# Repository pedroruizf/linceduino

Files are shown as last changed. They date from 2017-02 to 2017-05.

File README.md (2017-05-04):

# LINCEDUINO
Desarrollo de linceduino, ayuda electrónica del lince.
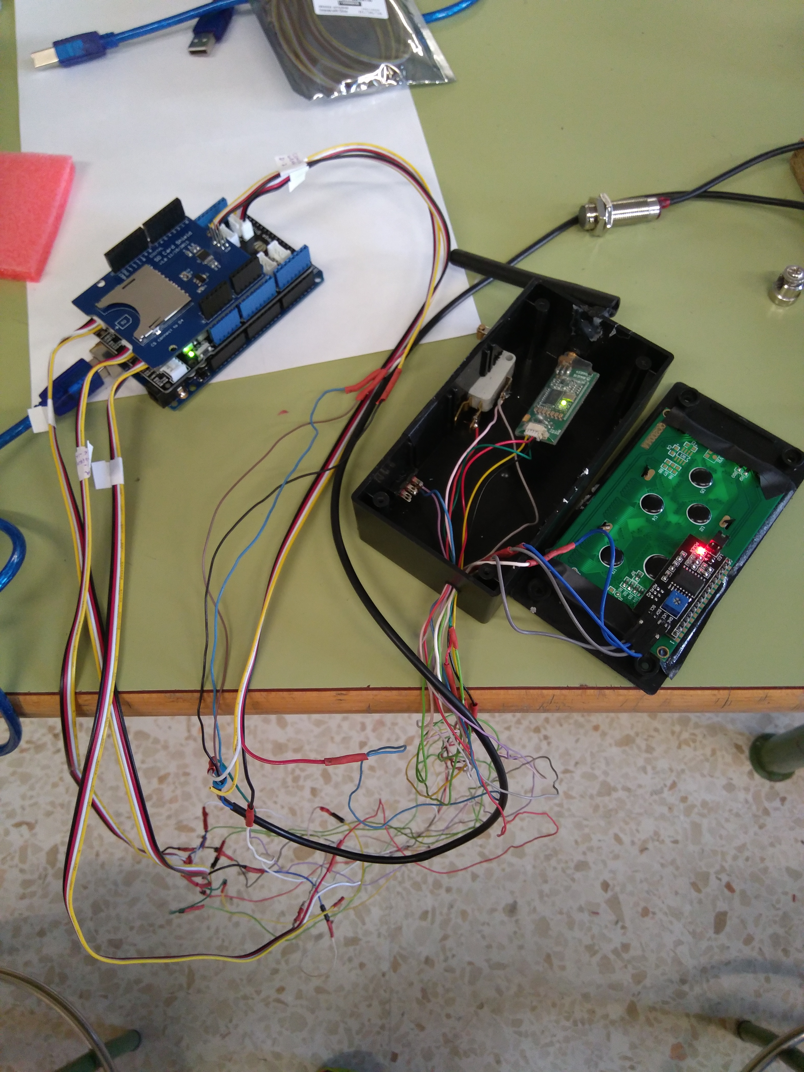
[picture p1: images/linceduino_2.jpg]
linceduino 2 linceduino2


## Objetivo

El objetivo de linceduino es proporcionar una herramienta que ayude al piloto y al equipo del LINCE a tener información en tiempo real y guardada en fichero de parámetros del vehículo como: tiempo transcurrido, velocidad instantánea, velocidad media, distancia, nº de vuelta y pulsación del botón de encendido de motor. Los datos se muestran en pantalla del piloto (lcd 20x4) se guardan en tarjeta SD y se transmiten mediante radiofrecuencia a PC.

## Hardware
Elementos físicos y conexionado:
- Arduino Mega.
- SD Shield.
- [Emisor de radiofrecuencia tipo 3DR Robotics](https://www.amazon.es/SODIAL-Telemetria-Quadcopter-Multirotor-robotica/dp/B0171NHADI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)   (con receptor a PC): rojo (5v), negro (gnd), amarillo (pin 17 RX2), verde (pin 16 TX2).
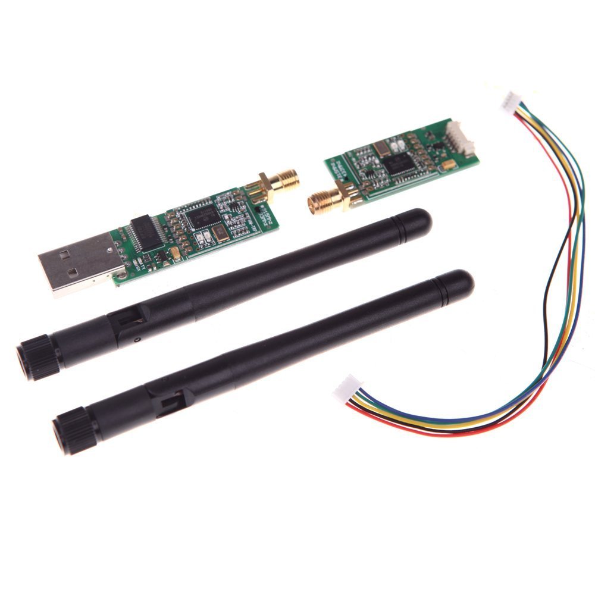
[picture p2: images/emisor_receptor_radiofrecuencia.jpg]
Emisor receptor radiofrecuencia

- LCD I2C 20x4: GND (gnd), VCC (5v), SDA (pin 20), SCL (pin 21).
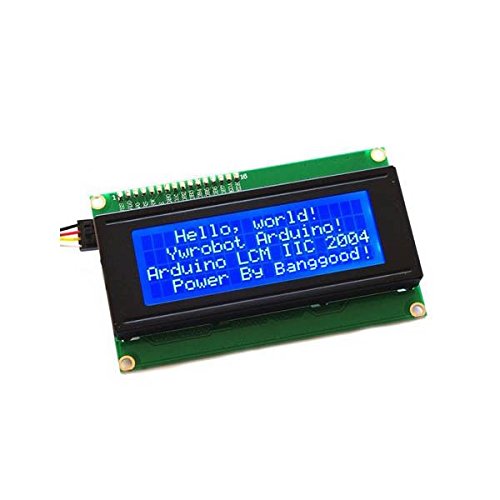
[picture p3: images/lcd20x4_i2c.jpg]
lcd 20x4 i2c lc2 20x4 i2c

- Pulsador de marcha con resistencia de 10 K en serie: pata de pulsador a 5V, la otra a pin 19, resistencia una pata a pin 19 y la otra a GND.
- Conmutador de grabación y resistencia de 10K: Conmutador común a pin 7, otra pata del conmutador a 5v, resistencia de 10 K a pin y la otra pata de la resistencia a GND.
- Sensor magnético Hall: Negro a pin 2, marrón a 5V y azul a GND.
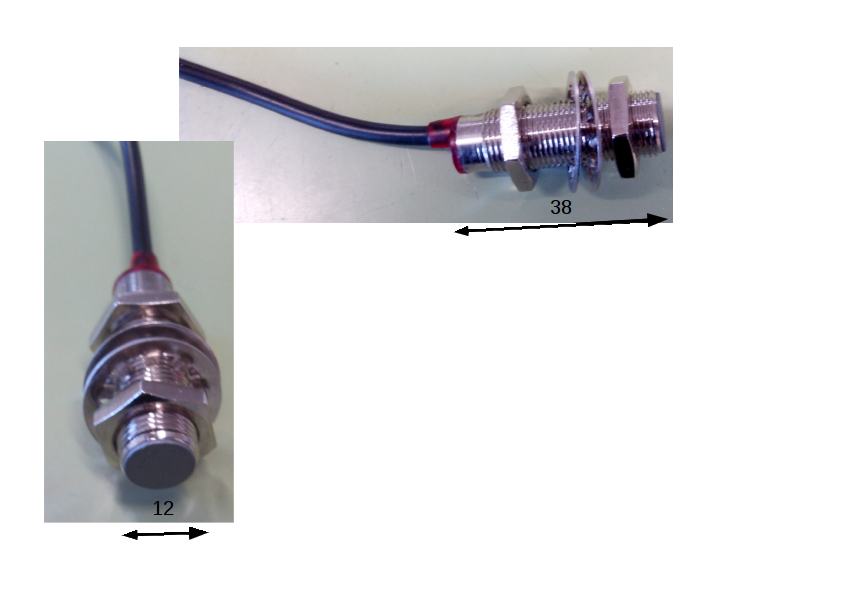
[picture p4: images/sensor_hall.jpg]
sensor hall

Además hemos comprado para realizar un conexionado más seguro un shield conectar y listo (tienda electan) con cables para que el conexionado de todos los elementos sea mucho más seguro.
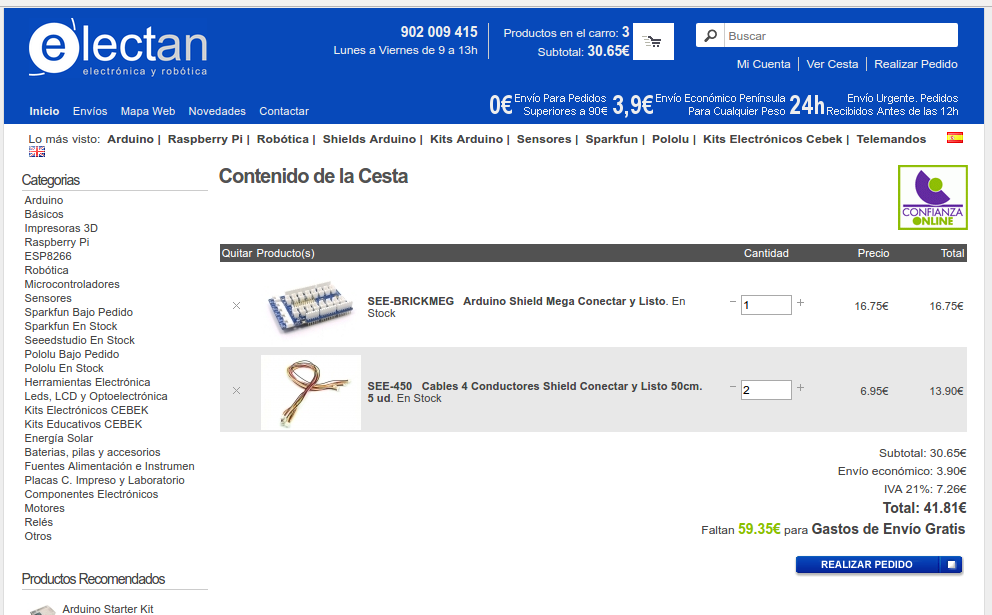
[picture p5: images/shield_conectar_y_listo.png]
Shield conectar y listo Shield Conectar y listo


### Montaje de Linceduino
<iframe width="854" height="480" src="https://www.youtube.com/embed/O8orDAbzBl0" frameborder="0" allowfullscreen></iframe>

## Software
Antes de nada tener un ordenador con ubuntu instalado.
Instalar en el las aplicaciones arduino, kst y Gtkterm, estas aplicaciones están en el centro de software.
Descripción de aplicaciones:
- Arduino: software para programar nuestro arduino Mega.
- Gtkterm: grabador y visualizador de comunicaciones por puerto serie, puerto por el que manda y recibe datos nuestro emisor y receptor de radiofrecuencia.
- KST: representador de datos en tiempo real a través de los datos recogidos en un fichero por Gtkterm.
En nuestro arduino además debemos de agregar una librería para poder operar con nuestro lcd 20x4 (20 columnas 2 filas) de tipo I2C (sólo necesita 4 cables, 2 de alimentación y 2 de datos).

### Programa de Arduino. Linceduino 2.2
~~~
#include <SPI.h>
#include <math.h>
#include <SD.h>
#include <Wire.h>  // Comes with Arduino IDE
#include <LiquidCrystal_I2C.h>
LiquidCrystal_I2C lcd(0x3F, 2, 1, 0, 4, 5, 6, 7, 3, POSITIVE);  // Set the LCD I2C address de 20x4

#define REFRESCO_SD 4 //Frecuencia de guardado
#define pinsd 4 // pin que marca el fabricante de SD Shield
Sd2Card card;// defino una variable card com Sd2CArd
float desarrollo=1492.6; // desarrollo de una vuelta del lince en mm
volatile float tiempopaso, tiempovuelta;//tiempo (hasta la activación del sensor y de una vuelta)
volatile float velocidad, velocidadm; //velocidades (instantánea y media)
volatile float distancia; //distancia recorrida desde que empieza a circular
volatile int lineasBuffer = 0; // lineas de buffer guardadas
volatile int nvueltas = 0; //vuelta de rueda
volatile bool marcha=false;// estado de pulsador de impulso
volatile long ultimamarcha=0;//tiempo que se pulso por ultima vez marcha
String minutos, segundos; //minutos y segundos desde el inicio
char s_string [10];
char m_string [10];
unsigned long tiempo1=0; //tiempo inicial
int vueltas; //vuelta del circuito
String buffer=""; // Almacenamiento temporal de datos recogidos de ISR, para la tarjeta SD
volatile int botonpulsado;// Botón para guardado
File dataFile; //Fichero para guardar datos
bool c = true; //Booleano para la representación

void setup() {

attachInterrupt(0, calculos, RISING);//pin de interrupción 2 arduino mega para sensor hall
attachInterrupt(4, calculosmarcha, CHANGE);//pin de interrupción 19 arduino mega: marcha
lcd.begin(20, 4); //iniciamos la pantalla lcd
lcd.setBacklight(1);
//lcd.backlight ();//da luz al fondo de pantalla de lcd
lcd.clear();
pinMode(pinsd, OUTPUT);
SD.begin(pinsd);//inicializa la SD (tiene que estar insertada) sólo lo hace una vez
lcd.setCursor(0,1);// pone el lcd en la posicion 0,1
if (card.init(SPI_HALF_SPEED, pinsd)) {    
  lcd.print("Tarjeta SD preparada");}
    // don't do anything more:
  //return;
 else {lcd.print("SD error o no inser.");}
lcd.setCursor (1,2); lcd.print ("(: VAMOS LINCE ;)");
delay (4000);
lcd.clear();
Serial2.begin (57600);//comunicacion por puerto serie2 de radiofrecuencia
//Serial.begin (9600);

}

void calculos() {
//Calcula los datos a representar
if (nvueltas==1) {tiempo1=millis();}
nvueltas++;
tiempovuelta=millis()-tiempopaso;//tiempo por vuelta
tiempopaso=millis();//tiempo desde que se produjo la interrupcion
velocidad=(desarrollo*3.6)/tiempovuelta; // (km/h), [mm/ms*3,6 para pasar a km/h]
velocidadm=(desarrollo*3.6*nvueltas)/(millis() - tiempo1);
distancia=(nvueltas*desarrollo)/1000000; //distancia total (km)
vueltas= int((distancia)/1.659)+1; // el circuito tiene 1659 m= 1.659 Km
//solo guarda en buffer y por tanto guarda en fichero cuando si se ha pulsado el boton select
if(botonpulsado==1 && nvueltas>2) {
guardabuffer();
}
}

void calculosmarcha() {
//Interrupción para pulsador 'marcha'
if ((millis()-ultimamarcha)>100 ) {
marcha=!marcha;
ultimamarcha=millis();
if(botonpulsado==1) {
guardabuffer();}
}
}

void guardabuffer(){
//Guarda los datos temporalmente en un buffer
   buffer += String(int((millis()-tiempo1)/1000));buffer += ";";
   buffer += nf(velocidad,2,2);buffer += ";";
   buffer += nf(velocidadm,2,2);buffer += ";";
   buffer += nf(distancia,2,2);buffer += ";";
   buffer += vueltas;buffer += ";";
   buffer += marcha;buffer += "\n";
   lineasBuffer++;
}

void guardasd(){
//Guarda el buffer en un archivo
//SD.begin(pinsd);//inicializa la sd debe estar insertada
dataFile = SD.open("log0.txt", FILE_WRITE);

if (dataFile) {
dataFile.print(buffer);
//lineasBuffer = 0;
//buffer = "";
dataFile.close();
lcd.setCursor(16,0);
c = !c;
if(c) {lcd.print("|");}

else {lcd.print("-");}
}
else {}
}

String nf(float n, int cifras, int decimales) {// la funcion nf tiene como entrada una variable float, el numero de cifras enteras, y el numero de cifras decimales
char numero [10];//creamos la variable tipo char numero de longitud 10
return dtostrf(n,(cifras+decimales+1),decimales,numero);//dtostrf convierte a cadena el valor float n, le pasamos el nº total de caracteres, el nº de decimales, y la variable donde se guarda en nuestro caso numero
//int punto = String(numero).indexOf("."); //calculamos la posicion del punto decimal
//String parte_entera = String(numero).substring(0,punto);//cortamos la parte entera de la variable numero y la guardamos en la variable parte_entera
//String parte_decimal = String(numero).substring(punto+1);//cortamos la parte decimal de la variable numero y la guardamos en la variable parte_decimal
//return parte_entera + "," + parte_decimal;//la funcion devuelve la union de la parte entera y la decimal separadas por coma, para ser tratada luego en una hoja de calculo
}

String tiempo() {
// Devuelve el tiempo de la forma ‘000:00’
dtostrf((millis()-tiempo1)/60000,3,0,m_string);//asigna a la variable m_string el numero de minutos dejandolo con tres enteros
dtostrf(((millis()-tiempo1) % 60000)/1000,1,0,s_string);
minutos = String(m_string);
segundos = String(s_string);
if (segundos.length() < 2) {segundos = "0" + segundos;}
return minutos + ":" + segundos;
}

void loop() {
//Bucle principal. Representa y reinicia variables

botonpulsado=digitalRead (7);// controla el guardado de datos con el conmutador
if (nvueltas==1) {tiempo1=millis();}
if (lineasBuffer >= REFRESCO_SD) {Serial2.print (buffer);guardasd();lineasBuffer = 0;buffer="";}

lcd.setCursor(0,0);
lcd.print("Vi=");
if((millis()-tiempopaso) < 3000) {if (velocidad<100) {
lcd.setCursor(3,0);
lcd.print(nf(velocidad,2,1));
}} //si la velocidad es > 100 no representa}
else {lcd.print(" 0.0");}

lcd.setCursor(8,0);
lcd.print("km/h");

lcd.setCursor(0,1);
lcd.print("Vm=");

if (velocidadm<100) {
lcd.setCursor(3,1);
lcd.print(nf(velocidadm,2,1));}

lcd.setCursor(8,1);
lcd.print("km/h");

lcd.setCursor(14,0);
if (botonpulsado==1) {lcd.print("G");}
else {lcd.print("N");}

lcd.setCursor(14,3);
if (vueltas<=9) {
lcd.print("V:");
lcd.setCursor(16,3);
lcd.print(vueltas);}
else {lcd.print("FINAL");}

lcd.setCursor(1,3);
lcd.print("d=");

lcd.setCursor(3,3);
lcd.print(nf(distancia,3,2));

lcd.setCursor(10,3);
lcd.print("km");

lcd.setCursor(1,2);
lcd.print("t=");

lcd.setCursor(3,2);
lcd.print(tiempo());

lcd.setCursor(14,1);
//lcd.print (marcha);
if((velocidad>100 || velocidadm>100) && nvueltas>2){lcd.print("ERROR");}
else{lcd.print("     ");}

delay(200);
}
~~~

## Manual de uso
Cuestiones a tener en cuenta a la hora de hacer funcionar a Linceduino.

### LCD
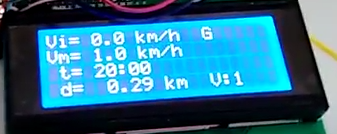
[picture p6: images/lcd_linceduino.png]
lcd linceduino 2 LCD linceduino

- 1ª Fila: Velocidad instántanea (Km/h), caracter de guardado (N o G) según como esté el conmutador de grabación
- 2ª fila: Velocidad media (Km/h), mensaje de "ERROR" si las velocidades medias o instantánea son superiores a 100 Km/h
- 3ª FIla: tiempo en h/m/s
- 4ª Fila: distancia (Km), nº de vuelta (indica final si es la última)

### Secuencia de uso
1. Se inserta SD limpia
2. Se alimenta a Linceduino. El tiempo empieza a contar en LCD pero no computa. Cuando la rueda da la primera vuelta (pasa por el sensor) el tiempo se pone a 0 y empieza a contar el verdadero tiempo de computo
3. Con el conmutador de guardado puedo elegir que guarde y transmita datos o que no lo haga, caracteres "N" o "G" del LCD

### Visualización de datos de SD
Antes de nada debemos de renombrar el archivo "lincebase.log" a "log0.txt" y copiarlo en la SD.

En el escritorio del PC debemos tener los archivos:
- "log.kst": fichero de muestra de datos de kst editado para linceduino
- "log0.txt": fichero que ha grabado linceduino en la SD, que copiamos en el escritorio.

Al abrir "log.kst" muestra los datos de "log0.txt" como en la figura.

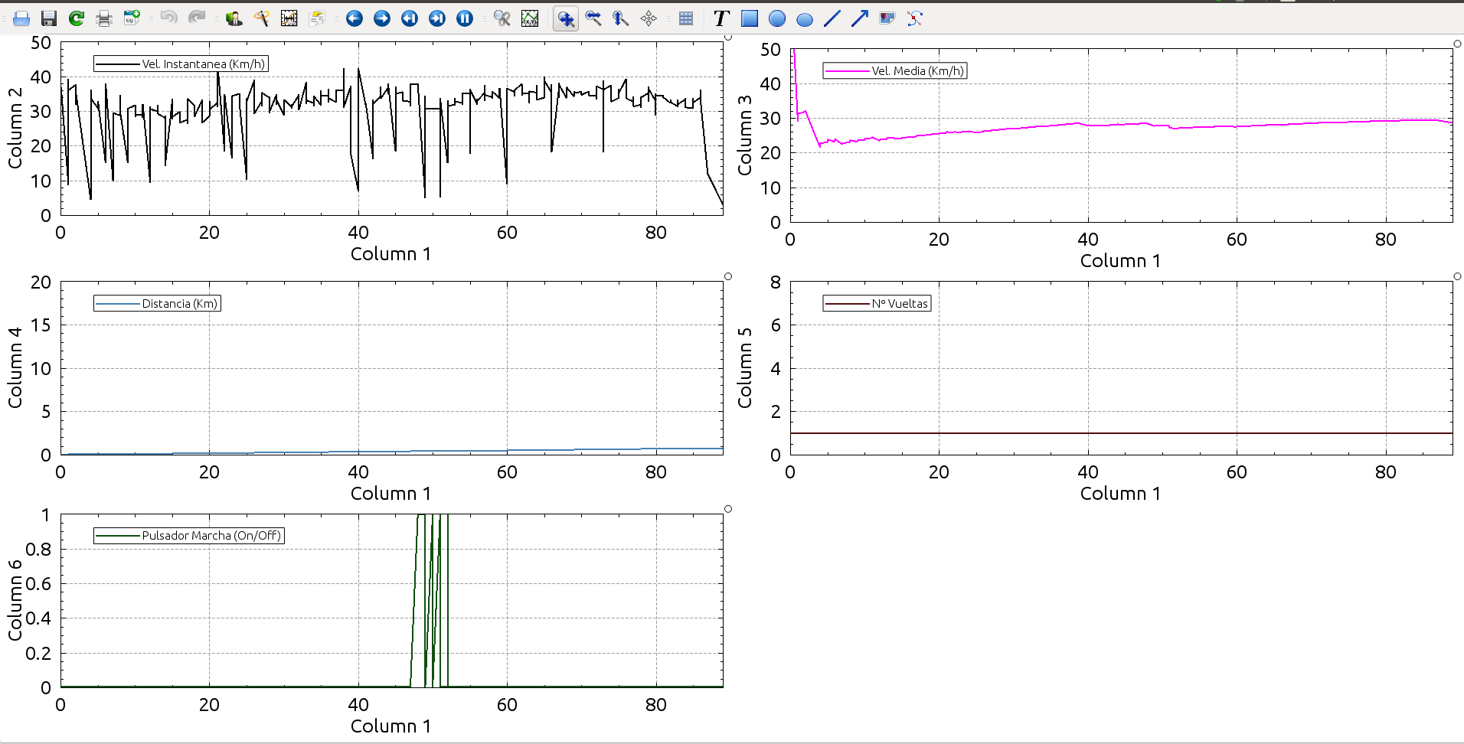
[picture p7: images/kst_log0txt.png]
kst con log0.txt


### Visualización de datos en tiempo real
- Antes de nada debemos de renombrar el archivo "lincebase.log" a "log0.txt" y copiarlo en el escritorio.
- Abrimos Gtkterm, que es un visualizador de datos en serie, y configuramos el puerto de comunicaciones a "/dev/ttyUSB0" en el menú del programa "Configuration>Port". "/dev/ttyUSB0" es el receptor de radiofrecuencia que tenemos en el PC. Ahora toca configurar dónde guardamos los datos en el menú del programa "Log>To file" y será en el archivo del escritorio "log0.txt".
- Abrimos con KST "log.kst".
- Ponemos en marcha linceduino y comienza la grabación de datos en SD y por radiofrecuencia si hemos seleccionado la grabación en el conmutador de grabado, y se empieza a mostrar los datos en gráficos en KST.

## Vídeos Linceduino
Os enlazamos veos de interés sobre linceduino.
- [Linceduino 1](https://www.youtube.com/watch?v=OVWAux1UXQ8)
- [Linceduino 2 dispositvos y telemetría](https://www.youtube.com/watch?v=JQcPb2iFT0I)
- [Software telemetría Linceduino 2](https://www.youtube.com/watch?v=axf5u40hDhU)
- [Montaje Linceduino 2](https://www.youtube.com/watch?v=O8orDAbzBl0)

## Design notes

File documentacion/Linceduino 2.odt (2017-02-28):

AYUDA ELECTRÓNICA PARA LINCE CON ARDUINO. LINCEDUINO.

Hardware definitivo

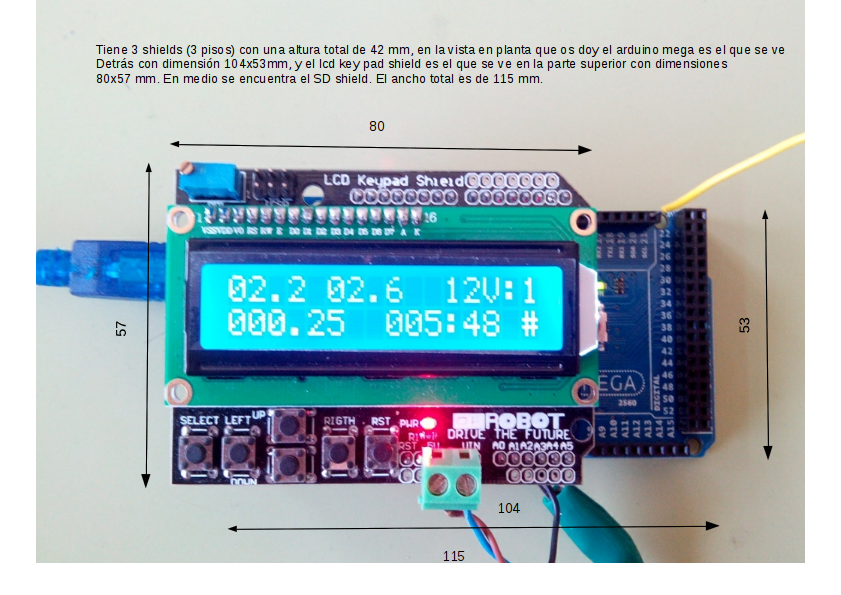
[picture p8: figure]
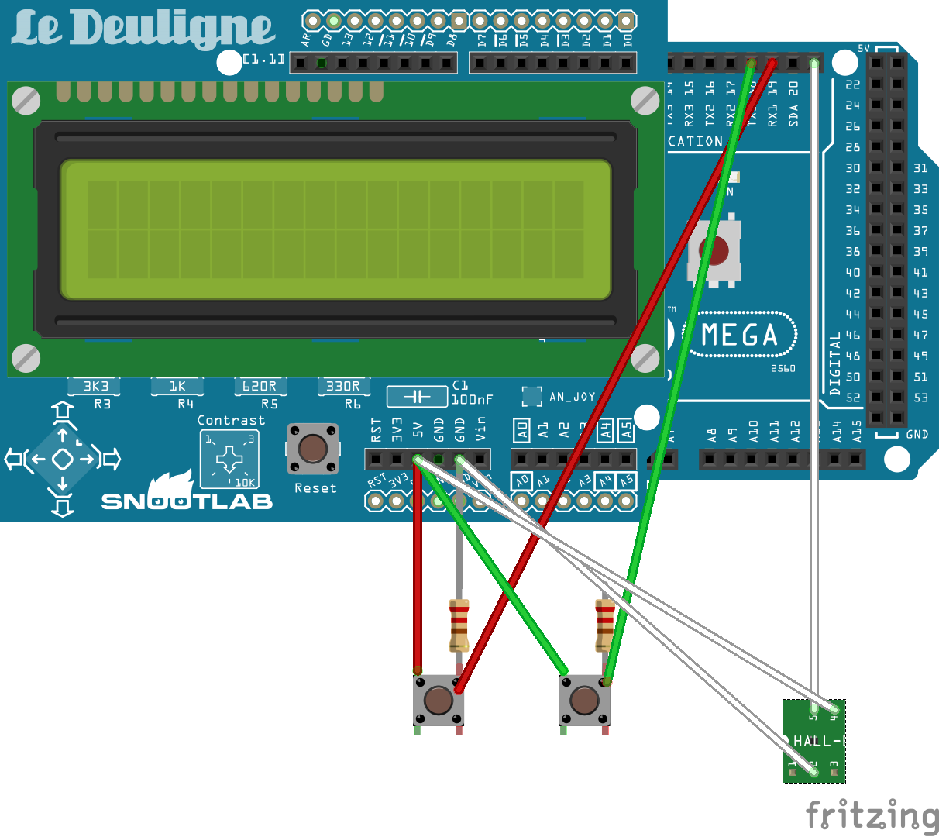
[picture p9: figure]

Descripción de conexionados

Pulsador NA de Marcha de motor: una pata a 5V, otra a pin 19 y resistencia 10 K y de resistencia de 10K a GND.

Pulsador NA de Paro de motor: una pata a 5V, otra a pin 18 y resistencia 10 K y de resistencia de 10K a GND.

Sensor Hall: cable marrón a 5V, cable azul a GND y cable negro a pin 21.

Software definitivo V 1.1

Código nuevo (con botonera para controlar guardado)

#include <LiquidCrystal.h>

#include <math.h>

#include <SD.h>

#define REFRESCO_SD 4 //Frecuencia de guardado

#define CS 4 // pin que marca el fabricante de SD Shield

LiquidCrystal lcd(8, 9, 4, 5, 6, 7);

float radio=236.82; // radio de la rueda en mm hay que poner la real del lince

volatile float tiempopaso, tiempovuelta;//tiempo (hasta la activación del sensor y de una vuelta)

volatile float velocidad, velocidadm; //velocidades (instantánea y media)

volatile float distancia; //distancia recorrida desde que empieza a circular

volatile int lineasBuffer = 0; // lineas de buffer guardadas

volatile int nvueltas = 0; //vuelta de rueda

volatile int marcha,paro;// estado de pulsadores de impulso o paro

String minutos, segundos; //minutos y segundos desde el inicio

char s_string [10];

char m_string [10];

unsigned long tiempo1=0; //tiempo inicial

int vueltas; //vuelta del circuito

String buffer=""; // Almacenamiento temporal de datos recogidos de ISR, para la tarjeta SD

volatile int botonpulsado=0;// Botón del lcdkeypad

File dataFile; //Fichero para guardar datos

bool c = true; //Booleano para la representación

void setup() {

attachInterrupt(2, calculos, RISING);//pin de interrupción 21 arduino mega para sensor hall

attachInterrupt(4, calculosmarcha, RISING);//pin de interrupción 19 arduino mega: marcha

attachInterrupt(5, calculosparo, RISING);//pin de interrupción 18 arduino mega: paro

lcd.begin(16, 2); //iniciamos la pantalla lcd

pinMode(CS, OUTPUT);

SD.begin(CS);//inicializa la SD (tiene que estar insertada) sólo lo hace una vez

}

void calculos() {

//Calcula los datos a representar

//if (nvueltas==1) {tiempo1=millis();}

nvueltas++;

tiempovuelta=millis()-tiempopaso;//tiempo por vuelta

tiempopaso=millis();//tiempo desde que se produjo la interrupcion

velocidad=(TWO_PI*radio*3.6)/tiempovuelta; // (km/h), [mm/ms*3,6 para pasar a km/h]

distancia=(nvueltas*TWO_PI*radio)/1000000; //distancia total (km)

vueltas= int((distancia)/1.626)+1; // el circuito tiene 1626 m= 1.626 Km

//solo guarda en buffer y por tanto guarda en fichero cuando si se ha pulsado el boton select

guardabuffer();

}

void calculosmarcha() {

//Interrupción para pulsador 'marcha'

marcha=1;

guardabuffer();

}

void calculosparo() {

//Interrupción para pulsador 'paro'

paro=1;

guardabuffer();

}

void guardabuffer(){

//Guarda los datos temporalmente en un buffer

if(botonpulsado==5) {

buffer += String(int((millis()-tiempo1)/1000));buffer += ";";

buffer += nf(velocidad,2,2);buffer += ";";

buffer += nf(velocidadm,2,2);buffer += ";";

buffer += nf(distancia,2,2);buffer += ";";

buffer += vueltas;buffer += ";";

buffer += marcha;buffer += ";";

buffer +=paro; buffer += "\n";

lineasBuffer++;

}

}

void guardadatos(){

//Guarda el buffer en un archivo

dataFile = SD.open("tele.txt", FILE_WRITE);

dataFile.print(buffer);

lineasBuffer = 0;

buffer = "";

dataFile.close();

lcd.setCursor(15,1);

c = !c;

if(c) {lcd.print("|");}

else {lcd.print("-");}

}

String nf(float n, int cifras, int decimales) {

char numero [10];

dtostrf(n,(cifras+decimales+1),decimales,numero);

int punto = String(numero).indexOf(".");

String parte_entera = String(numero).substring(0,punto);

String parte_decimal = String(numero).substring(punto+1);

return parte_entera + "," + parte_decimal;

}

String tiempo() {

// Devuelve el tiempo de la forma ‘000:00’

dtostrf((millis()-tiempo1)/60000,3,0,m_string);

dtostrf(((millis()-tiempo1) % 60000)/1000,1,0,s_string);

minutos = String(m_string);

segundos = String(s_string);

if (segundos.length() < 2) {segundos = "0" + segundos;}

return minutos + ":" + segundos;

}

void leebotones (int valorsensor) {

// A cada botón le corresponde un rango de valores

if (valorsensor <1000 || valorsensor>1100) {botonpulsado=0;} //ningun boton pulsado

if (valorsensor<10) { botonpulsado=1;}

if (valorsensor>90 && valorsensor<110) {botonpulsado=2;}

if (valorsensor>200 && valorsensor<300) {botonpulsado=3;}

if (valorsensor>400 && valorsensor<450) {botonpulsado=4;}

if (valorsensor>600 && valorsensor<650) {botonpulsado=5;SD.begin(CS);} //boton select

}

void loop() {

//Bucle principal. Representa y reinicia variables

leebotones(analogRead(0)); //comprueba que botón ha sido pulsado o sino se ha pulsado (0)

if (nvueltas==1) {tiempo1=millis();}

if (lineasBuffer >= REFRESCO_SD) {guardadatos();}

velocidadm=(TWO_PI*radio*3.6*nvueltas)/(millis() - tiempo1);

lcd.setCursor(0,0);

if((millis()-tiempopaso) < 3000) {if (velocidad<100) {lcd.print(nf(velocidad,2,1));}} //si la velocidad es > 100 no representa}

else {lcd.print(" 0,0");}

lcd.setCursor(5,0);

if (velocidadm<100) {lcd.print(nf(velocidadm,2,1));}

lcd.setCursor(15,0);

if (botonpulsado==5) {lcd.print("G");}

else {lcd.print("N");}

//lcd.setCursor(14,0);

//lcd.print(marcha);

//lcd.setCursor(15,0);

//lcd.print(paro);

lcd.setCursor(10,0);

if (vueltas<=9) {

lcd.print("V:");

lcd.print(vueltas);}

else {lcd.print("FINAL");}

lcd.setCursor(0,1);

lcd.print(nf(distancia,3,2));

lcd.setCursor(7,1);

lcd.print(tiempo());

lcd.setCursor(14,1);

if(velocidad>100 || velocidadm>100 ){lcd.print("E");}

else{lcd.print(" ");}

marcha=0;

paro=0;

delay(200);

}

MANUAL PARA LINCEDUINO

- Cuando se inicia (reset o alimentación) cuenta el tiempo. Lo reinicia cuando se mueve.
- Para grabar datos hay que darle al botón “select”. Para que deje de grabar datos hay que pulsar cualquier botón que no sea “select” o “reset” (se puede hacer en box). Es conveniente hacerlo con el vehículo parado, para asegurar el cierre del fichero de datos.
- Antes de la carrera:
  - La persona que pilota pulsa reset (reinicio del tiempo) y luego select (grabación).
  - Linceduino empezará a grabar con un tiempo inicial (desde el reinicio hasta empezar a moverse) que hay que quitar de los tiempos grabados.
- LCD (Pantalla) de Linceduino

1ª Fila

V. Instantánea [km/h] 00,0 (2 enteros 1 decimal) | V. Media [km/h] 00,0 (2 enteros 1 decimal) | Nº de vuelta (V:0) En la vuelta final pone FINAL | Grabación (último) N: grabado inactivo G: grabado activo

2ª Fila

Distancia [km] 000,00 (3 enteros 2 decimales) | Tiempo [min:s] 000,00 (3 enteros 2 decimales) | Error de sensor (penúltimo) E: error del sensor [Blanco]: sin error | Animación de grabación (último) [Animación]: graba

HOJA DE CÁLCULO

Archivo TELE.TXT vinculado a hoja de cálculo de datos, hay otra hoja de gráfico y otra de cabeceras del gráfico.

AYUDAS E INVESTIGACIONES

Ideas de Daniel Segura (Ingeniero Informático) sobre buffer y nuestro programa no hay nada metido en el programa

1) Las ISR (rutinas de tratamiento de interrupciones) (calculos() en el codigo) han de ser de codigo muy ligeras, la que se está usando es muy lenta, ya que dentro de la ISR hasta se graba en la tarjeta SD , haciendo una llamada a otra subrutina "guardadatos()".

2) Las variables globales que vayan a ser actualizadas dentro de una ISR deben ser declaradas como "volatile", para garantizar que se actualizan correctamente.

En palabras de los tipos de Arduino:

"About Interrupt Service Routines

ISRs are special kinds of functions that have some unique limitations most other functions do not have. An ISR cannot have any parameters, and they

shouldn't return anything.

Generally, an ISR should be as short and fast as possible. If your sketch uses multiple ISRs, only one can run at a time, other interrupts will be ignored (turned off) until the current one is finished. as delay() and millis() both rely on interrupts, they will not work while an ISR is running.

delayMicroseconds(), which does not rely on interrupts, will work as expected.

Typically global variables are used to pass data between an ISR and the main program. To make sure variables used in an ISR are updated correctly, declare them as volatile. "

Bien, como te dije a mi eso de escribir en SD tol rato pos como que no me gustaba un pelo, mejor ir acumulando informacion en memoria (buffer) y volcar a SD cuando el buffer se llene. Dicho buffer lo hemos tirado a lo mas sencillo posible, es un String al que se van encadenando los valores recogidos en "calculos()" añadiendo al final de cada secuencia un salto de linea.

La constante REFRESCO_SD (#define REFRESCO_SD 2) indica el tamaño del buffer en líneas, cuando se llene, entonces dentro de loop() y no en la ISR se llamará a la función de "guardaDatos()", que se encargará en un solo paso de volcar toda la informacion a la SD.

OJO: puedes jugar con la variable REFRESCO_SD (para minimizar el numero de volcados a SD) aumentando su valor, pero arduino solo escribe realmente en la SD cuando se cierra el fichero, que en el código se produce cuando se llena el buffer, asi que no pongas un buffer muy grande, porque o bien te quedarás sin memoria ó sin que se haya terminado de rellenar el buffer y no se vuelque a la SD. Yo lo he dejado en cada par de vueltas, lo realmente interesante es que hemos sacado del codigo de la ISR la grabacion de datos a la SD.

La digestión del programa sería tal que así:

Las llamadas a la ISR calculos() lanzan un guardado de los datos al buffer (hemos creado una funcion guardabuffer() a tal efecto), esto es, graba a memoria y no en la SD

// La ISR llama a guardabuffer();

void calculos() {

nvueltas++;

vueltas=(distancia)/1.626; // el circuito tiene 1626 m= 1.626 Km

guardabuffer(); //Actualiza el buffer (en memoria, no en SD)

}

// guardabuffer actualiza la variable global buffer encadenandole los valores al final

void guardabuffer(){

buffer += nf(velocidad,2,2);buffer += ",";

buffer += nf(velocidadm,2,2);buffer += ",";

buffer += nf(distancia,2,2);buffer += ",";

buffer += nf(((millis()-tiempo1)/1000),2,2);buffer += "\n";

lineasBuffer++; // variable de control de tamaño del buffer

}

En el bucle principal se chequea la condicion del buffer lleno, si lo está se llama a guardadatos

void loop() {

if (nvueltas==1) {tiempo1=millis();}

//Aqui se llama a guardadatos() si el BUFFER esta lleno

if (lineasBuffer >= REFRESCO_SD) {

guardadatos();

}

guardadatos, ahora queda mucho más escueta, ya que solo tiene que guardar el buffer, que es un string engordado,

void guardadatos(){

dataFile=SD.open("tele.txt", FILE_WRITE); // Creamos archivo de texto

if(dataFile){

dataFile.print(buffer); //Almacenamos el contenido del buffer

lineasBuffer=0; //Reseteamos el numero de lineas usadas del buffer

buffer=""; // Limpiamos el buffer y a empezar de nuevo cuando se vuelva a invocar la ISR

dataFile.close(); // Cerramos la escritura dentro del archivo <- AQUI ES REALMENTE CUANDO SE GRABA LA INFORMACIÓN

Fale, esta es mas o menos la idea que tenia en mente cuando hablamos, te adjunto el codigo, que no puedo probar, pero que compilar compila :).

En principio debería ir mejor, no he tocado nada que no fueren los datos, nada de nada de la LCD y tal, porque en los manuales de arduino viene tal y como está puesta, nosotros lo haciamos en Renesas con temporizadores que lanzaban una interrupción cada determinado intervalo de tiempo y actualizabas en su ISR la pantalla y así no andabas constantemente revisando la pantalla en el bucle principal.

Ojo, los buffers de verdad son toda una infraestructura soportada por el sistema operativo (o librerias) nosotros hemos abusao del lenguaje pa hacer esto, que no es ni de coña un buffer de verdad, pero para entendernos creo q vale ¿no?.

El codigo lo llevas adjunto, o bien le puedes echar un ojo aquí (https://github.com/danudoni/algo/blob/master/algo.ino)

Espero haber sido de ayuda. Un abrazo

Especificaciones de Linceduino e-mails de Manuel Barbero.

Especificaciones 2

CARACTERÍSTICAS DESEABLES PARA EL SISTEMA LINCEDUINO:

- Velocidad instantánea actual en km/h

- Velocidad media en km/h

- Distancia recorrida en kilómetros medida desde la salida del Lince, con dos cifras decimales. Éste dato se puede calcular a partir de la velocidad media y el tiempo transcurrido.

- Tiempo transcurrido en minutos y segundos desde la salida del Lince.

- Indicador en el que se lea "VUELTA Nº " y a continuación 1, 2, ... hasta 9, y al llegar a la última vuelta, la número 10, cambiaría la indicación a "VUELTA FINAL". Éste dato se calcularía en función del tiempo transcurrido desde la salida y del hecho de que cada vuelta tiene una longitud de 1,63 km.

- Pulsador de Reset.

Hemos valorado todos éstos datos como muy convenientes para facilitar la función del piloto.

En el caso ideal, y en el caso de que el display fuese muy pequeño para que se mostrase simultáneamente toda ésta información, se podría considerar dos displays.

- El autoreset a los 5 segundos de inactividad, no es deseable, porque puede darse el caso (por desgracia, mas de lo deseable), de que en competición, el vehículo se pare por avería instantánea, y que vuelva a arrancar. En éste caso, el tiempo de parada cuenta para contabilizar la velocidad media. Pienso que una posible idea podría ser colocar otro pulsador de parada, que, en condiciones normales, el piloto pulsaría al cruzar la línea de meta, con lo que los datos al pulsar éste pulsador se quedarían "congelados", tanto la velocidad media, distancia, tiempo e indicación "VUELTA FINAL".

- El pulsador de reset debería resetear todo el sistema, pero no debería iniciar el contador de tiempo hasta que el vehículo no empiece a moverse. El motivo es que el coche, al estar en la línea de salida, tiene dos minutos para salir. En parte de ese tiempo, el piloto hace una checklist, pero la velocidad media y el tiempo debería comenzar a contar cuando el coche empiece a moverse.

- Los decimales, serían uno para las velocidades, dos para la distancia (en kilómetros), el tiempo en minutos y segundos.

Especificaciones 1

Te comento los datos sobre la rueda del Lince que me pediste.

Aquí tienes un enlace a una buena imagen del Lince en el que se le ve la rueda delantera izquierda. Si te fijas, a eso de las 1, usando lenguaje de los pilotos, verás en un radio el imán del medidor de velocidad de bicicleta:

http://2.bp.blogspot.com/-qARpL4smn-c/UbcLVnt5eVI/AAAAAAAAC6w/REsKGfDmiBA/s1600/Lince-1.jpg

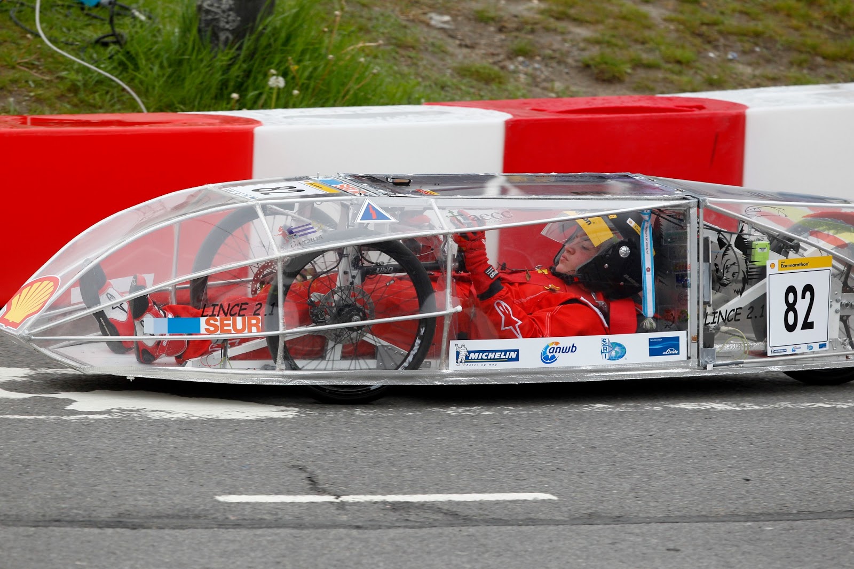
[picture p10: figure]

La llanta es de 16 pulgadas (40,64 cm de diámetro). La rueda totalmente montada con el neumático, y con una presión de 6kg/cm2, tiene un desarrollo de 1,498 m.

Éste desarrollo puede variar con la presión de inflado y con el peso total coche-piloto. Ante ésta variabilidad, yo te pediría, si fuese posible, que el programa pudiese preguntar y guardar en memoria el desarrollo real en cada momento, en cada configuración.

Una cuestión que me preocupa es el tiempo de respuesta del medidor de velocidad, es decir, que ante una velocidad estable, cuando ésta cambia, cuánto tiempo necesita el medidor para mostrar la nueva velocidad. Nuestro límite está en el tiempo de respuesta de los medidores de velocidad de bicicleta, que tienen un tiempo de 3 segundos (ésto es demasiado para nuestras necesidades). Por lo que sería necesario cuantificarlo en el ARDUINO.

Al depender el tiempo de respuesta del tiempo por revolución de la rueda junto con otros parámetros debidos al hardware del sistema y al software del mismo, nosotros intentamos bajar el tiempo de respuesta del medidor de bicicleta aumentando el número de imanes instalados en la rueda. Llegamos a pensar en poner 10, con lo que la indicación de la velocidad del medidor, para 25km/h reales hubiese sido 250km/h, con lo que el piloto lo único que debería imaginarse es la coma. No pudimos hacerlo, porque habría que variar el desarrollo introducido en el medidor, y los límites que traen esos aparatos no nos dejaban poner el desarrollo resultante. Lo digo por si al medir el tiempo de respuesta, si éste fuese alto, siempre se podría poner no un imán, sino dos o tres. En fin, son solo ideas fruto de nuestra experiencia, por si os valen.

Es importante que el sistema disponga de un pulsador que el piloto pueda pulsar cuando el vehículo esté parado en la línea de salida, para resetear la velocidad media y que comience a mostrar los parámetros de velocidad instantánea y media al comenzar a moverse.

Pruebas con reed en la Red

ver video http://www.youtube.com/watch?v=KNSgAHnP2wM

Nuestras Pruebas e Implementaciones para el Cálculo de Velocidad Media e Instántánea

La Lorenzina.

Horquilla portátil para realizar pruebas de ruedas. By Lorenzo Olmo.

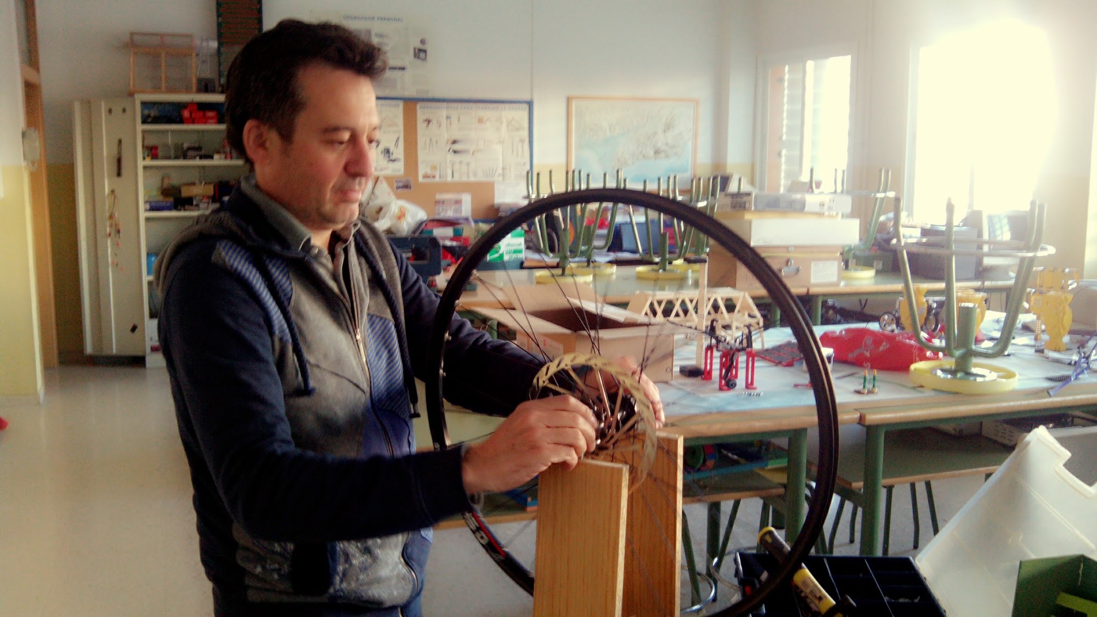
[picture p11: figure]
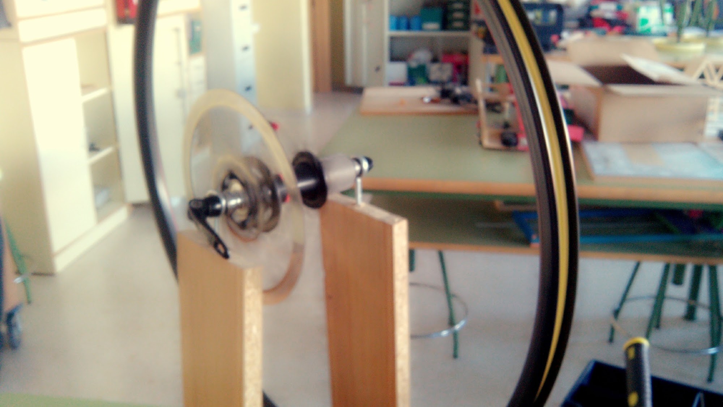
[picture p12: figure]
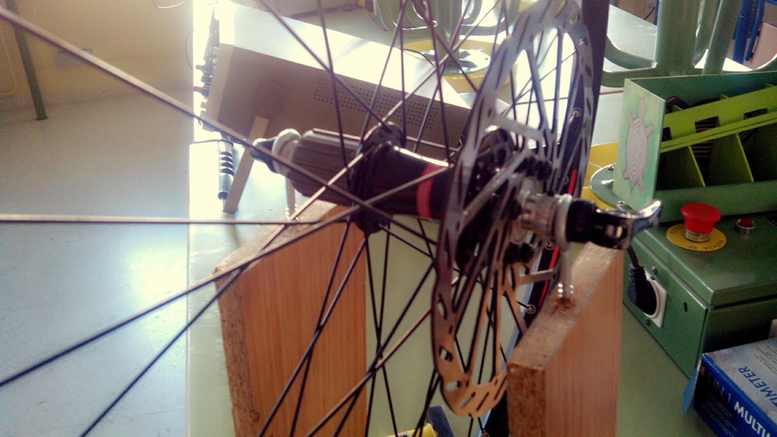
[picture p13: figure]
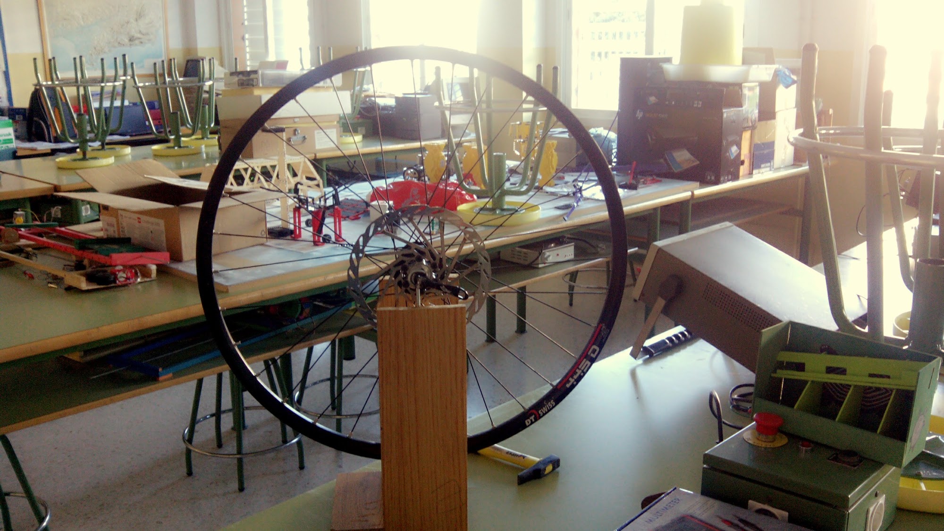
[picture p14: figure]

Programación

Ideas:

Podemos usar un sólo imán y sabiendo el desarrollo de la rueda y el tiempo por vuelta lo tenemos todo. El usar un sólo imán es por reducir errores de cálculo a la hora de colocar más imanes.

En realidad estamos usando un sensor Hall, que cuando está un campo magnético cerca de él (<10 mm) genera una señal eléctrica en el pin de 0.

Velocidades media e instantánea con LCD

/Incluimos la librería de LCD que trae arduino

#include <LiquidCrystal.h>

//Indicamos los pins que vamos a usar para

//comunicarnos con la pantalla

//En mi caso, al usar una lcd shield los botones

//son los siguientes

LiquidCrystal lcd(8, 9, 4, 5, 6, 7);

//Creamos una constante para tomar

//indicar a que pin está conectado

//const int sensoranalogico = 0;

//Creamos una variable para almacenar los

//valores tomados por los botones

int valorsensor = 0;

unsigned long tiempototal;

unsigned long tiempoparcial;

int vuelta=1498;//mm por vuelta

float velocidadactual;

float velocidadmedia;

int nvueltas = 0;

int pin=52;

//Inicia el void setup que solo se ejecuta

//una vez

void setup() {

//iniciamos la pantalla lcd y le

//indicamos el número de columnas x el número de filas

lcd.begin(16, 2);

pinMode (pin,INPUT);//pone de entrada el pin 52

}

//Inicia el loop que se ejecutará

//mientras el arduino esté conectado

void loop() {

velocimetro();

}

void velocimetro(){

tiempototal=millis();

tiempoparcial=(pulseIn (pin,LOW))/1000;//ms por vuelta

velocidadactual=(vuelta/tiempoparcial)*3.6;// vel. instantanea

if(tiempoparcial!=0){nvueltas = nvueltas+1;}

velocidadmedia = (nvueltas*vuelta*3.6)/tiempototal;

lcd.setCursor(0,0);

lcd.print("Vel.Inst: ");

lcd.print (velocidadactual);

lcd.setCursor(0,1);

lcd.print("Vel.Med: ");

lcd.print (velocidadmedia);

}

Velocidades media e instantánea segunda implementación

unsigned long tiempototal;

unsigned long tiempoparcial;

int vuelta=1498;//mm por vuelta

float velocidadactual;

float velocidadmedia;

int nvueltas = 0;

int pin=7;

void setup () {

Serial.begin(9600);

pinMode (pin,INPUT);

}

void monitoriza () {

//Serial.print ("Tiempo total (s):...");

//Serial.println (tiempototal);

//Serial.print ("Tiempo parcial (s):...");

//Serial.println (tiempoparcial);

Serial.print ("Vel. Ins (km/h):");

Serial.println (velocidadactual);

Serial.print ("Vel. Med (km/h):");

Serial.println (velocidadmedia);

//delay (1000);

}

void loop () {

tiempototal=millis();

tiempoparcial=(pulseIn (pin,LOW))/1000;//ms por vuelta

velocidadactual=(vuelta/tiempoparcial)*3.6;// vel. instantanea

if(tiempoparcial!=0){nvueltas = nvueltas+1;}

velocidadmedia = (nvueltas*vuelta*3.6)/tiempototal;

monitoriza();

}

Velocidades media e instantánea primera implementación

unsigned long tiempototal;

unsigned long tiempoparcial;

float cuartovuelta=70.686;//mm por 1/4 de vuelta en un disco de 9cm de diam.

float velocidadactual;

float velocidadmedia;

int ncuartos = 0;

int pin=7;

void setup () {

Serial.begin(9600);

pinMode (pin,INPUT);

}

void monitoriza () {

//Serial.print ("Tiempo total (s):...");

//Serial.println (tiempototal);

//Serial.print ("Tiempo parcial (s):...");

//Serial.println (tiempoparcial);

Serial.print ("Vel. Ins (km/h):");

Serial.println (velocidadactual);

Serial.print ("Vel. Med (km/h):");

Serial.println (velocidadmedia);

//delay (1000);

}

void loop () {

tiempototal=millis();

tiempoparcial=(pulseIn (pin,LOW))/1000;//ms por 1/4 de vuelta

velocidadactual=(cuartovuelta/tiempoparcial)*3.6;// vel. instantanea

if(tiempoparcial!=0){ncuartos = ncuartos+1;}

velocidadmedia = (ncuartos*cuartovuelta*3.6)/tiempototal;

monitoriza();

}

Órdenes usadas:

millis()

Descripción:

Devuelve el tiempo en milisegundos transcurridos desde que se arranco la placa Arduino con el programa actual. Este número de desbordará (volverá a cero), despues de aproximadamente 50 días.

Devuelve:

Tiempo en milisegundos desde que el programa se inició (long sin signo (unsigned long))

Ejemplo:

unsigned long time;

void setup(){
Serial.begin(9600);
}
void loop(){
Serial.print("Tiempo: ");
time = millis();
//Imprime el tiempo desde que se inició el programa
Serial.println(time);
// espera un segundo para no enviar demasiados datos
delay(1000);
}

Consejo:

Ten en cuenta que el parametro que devuelve millis() es un long sin signo por lo que pueden producirse errores si el programador intenta llevar a cabo operaciones matemáticas con otros tipos de dato como enteros.

pulseIn()

Descripción:

Lee un pulso (ya sea HIGH —alto— o LOW —bajo—) en un pin. Por ejemplo, si value es HIGH, pulseIn() espera a que el pin sea HIGH, empieza a cronometrar, espera a que el pin sea LOW y entonces detiene la medida de tiempo. Devuelve la anchura del pulso en microsegundos. Interrumpe la medida y devuelve 0 si el pulso no ha comenzado en un tiempo especificado.

La medida del tiempo en esta función ha sido determinada de forma empírica y está sujeta a errores en pulsos largos. Funciona correctamente en pulsos con una anchura de 10 microsegundos a tres minutos.

Sintaxis:

pulseIn(pin, value)

pulseIn(pin, value, timeout)

Parámetros:

pin: el número del pin en el que se realiza la medida del pulso. (int)

value: tipo de pulso. Puede ser HIGH (http://arduino.cc/es/Reference/Constants) o LOW (http://arduino.cc/es/Reference/Constants). (int)

timeout (opcional): el tiempo en microsegundos máximo a esperar antes de que se inicie el pulso. (unsigned long)

Devuelve:

el ancho del pulso (en microsegundos) ó 0 si el pulso no ha empezado antes del timeout (unsigned long)

Ejemplo

int pin = 7;
unsigned long duracion;

void setup()
{
pinMode(pin, INPUT);
}

void loop()
{
duracion = pulseIn(pin, HIGH);
}

unsigned long

Descripción:

Las variable long sin firmar (unsigned long) son variables extendidas para almacenar números, y almacenar 32 bits (4 bytes). Por el contrario que las variables long estándar, las unsigned long no almacenan números negativos, haciendo que su rango sea de 0 a 4,294,967,295 (2^32 - 1).

Ejemplo:

unsigned long tiempo;

void setup()
{
Serial.begin(9600);
}

void loop()
{
Serial.print("Tiempo: ");
tiempo = millis();
//imprime el tiempo desde el inicio del programa
Serial.println(tiempo);
// espera un segundo para no enviar cantidade masivas de datos
delay(1000);
}

Sintáxis:

unsigned long var = val;

var - el nombre de tu variable long

val - el valor que asignas a tu variable long

Ver también:

byte (http://arduino.cc/es/Reference/Byte)

int (http://arduino.cc/es/Reference/Int)

unsigned int (http://arduino.cc/es/Reference/UnsignedInt)

long (http://arduino.cc/es/Reference/Long)

Variable Declaration (http://arduino.cc/en/Reference/VariableDeclaration)

LCD y Arduino

Se trata de mostrar en un LCD 16x2 (16 caracteres y 2 filas) la velocidad instantanea y la media del LINCE.

Lcd 16x2 sin shield

http://www.proyectosarduino.com.ar/conectando-una-pantalla-lcd-a-arduino/

LCD 16x2 key pad Shield

http://multitechnologyblog.wordpress.com/2012/06/15/arduino-tutorial-lcd-keypad-shield-hola-mundo-codigo/

http://www.ajpdsoft.com/modules.php?name=News&file=article&sid=627

El programa siguiente está basado en la siguiente web

http://itmanageratschool.blogspot.com.es/2012/05/lcd-shield-with-keypad-para-arduino.html

Programa para presentar información en la lcd keypad shield y aprovechar los botones

//Incluimos la librería de LCD que trae arduino

#include <LiquidCrystal.h>

//Indicamos los pins que vamos a usar para

//comunicarnos con la pantalla

//En mi caso, al usar una lcd shield los botones

//son los siguientes

LiquidCrystal lcd(8, 9, 4, 5, 6, 7);

//inciamos el valor del sensor analogico 0 a 0

int valorsensor = 0;

//Inicia el void setup que solo se ejecuta

//una vez

void setup() {

//iniciamos la pantalla lcd y le

//indicamos el número de columnas x el número de filas

lcd.begin(16, 2);

//Imprimimos por pantalla la frase Prueba botones

lcd.print("Prueba botones");

//Movemos el cursor a la segunda línea

lcd.setCursor(0, 2);

//Ponemos un mensaje en la segunda línea

//que nos pide que pulsemos un botón

lcd.print("Pulse un boton");

}

//Inicia el loop que se ejecutará

//mientras el arduino esté conectado

void loop() {

//Recogemos el valor en el pin analógico

//que nos dirá que botón hemos pulsado

valorsensor = analogRead(0);

//En el debuggin hemos visto que al no tener ningún botón

//pulsado los valores devueltos están entre

//1020 y 1025 por lo que cuando se den valores distintos

//a ese rango se ejecutará lo que hay dentro del if

if (valorsensor <1000 || valorsensor>1100) {

//llamamos a la función limpiar línea que veremos

//un poco más abajo

limpiarLinea();

}

if (valorsensor<10) {

lcd.setCursor(0,2);

lcd.print ("derecha");

}

if (valorsensor>90 && valorsensor<110) {

lcd.setCursor(0,2);

lcd.print ("arriba");

}

if (valorsensor>200 && valorsensor<300) {

lcd.setCursor(0,2);

lcd.print ("abajo");

}

if (valorsensor>400 && valorsensor<450) {

lcd.setCursor(0,2);

lcd.print ("izquierda");

}

if (valorsensor>600 && valorsensor<650) {

lcd.setCursor(0,2);

lcd.print ("select");

}

}

//Esta función la llamamos cuando queremos borrar

void limpiarLinea(){

//Colocamos el cursor la principio de la segunda

//línea

lcd.setCursor(0, 2);

//Con este bucle recorremos toda la línea y la ponemos

//en blanco

for (int i = 0; i < 16; i = i + 1) {

lcd.print(" ");

}

//Volvemos a colocar el cursor

//al principio de la línea

//para cuando volvamos a escribir algo

//salga desde el principio de la línea

lcd.setCursor(0, 2);

}

Trabajar con Tarjeta SD para grabar datos

Se trataría de grabar los pulsos que da el piloto para el encendido del motor y la velocidad en ese momento y el tiempo transcurrido total, todo separado por comas para ser tratado en una hoja de cálculo (documento csv) y representarse gráficamente par dar una telemetría.

http://tallerarduino.com/2012/11/29/arduino-tutorials-cap7-uso-de-las-memorias-sd/

http://zygzax.com/2013/12/14/escribir-datos-en-una-tarjeta-sd-con-arduino-modulo-microsd-y-ethernet-shield/

Ejemplo de Software para grabar un texto en SD y Monitor serie

// Programa hecho por David Alvarez Medina (0xDA_bit) para tallerarduino.wordpress.com

// Escritura de una frase en una tarjeta SD

#include <SD.h> // Importamos libreria

// Declaracion de pins y variables de uso interno

int CS=10;

String dataString;

File dataFile;

void setup(){

Serial.begin(9600); // Establecemos comunicacion serie

Serial.println("Iniciando lectura tarjeta SD"); // Texto informativo

pinMode(CS, OUTPUT); // Declaramos el pin ChipSelect como salida

if(!SD.begin(CS)){ // Si no hay tarjeta o esta mal...

Serial.println("Tarjeta erronea o no insertada"); // Texto informativo

return;

}

Serial.println("Tarjeta OK"); // Texto informativo

}

void loop(){

dataString="tallerArduino Tutorial numero 7"; // Actualizamos la linea que guardaremos en el archivo de texto

dataFile=SD.open("log.txt", FILE_WRITE); // Creamos archivo de texto

if(dataFile){

dataFile.println(dataString); // Excribimos el contenido de "dataString" dentro del archivo de texto

dataFile.close(); // Cerramos la escritura dentro del archivo

Serial.println(dataString); // Texto informativo

}

else{

Serial.println("Escritura erronea... "); // Texto informativo

}

delay(2000); // Delay

}

Materiales

Arduino

Arduclema (http://tienda.ray-ie.com/basados-en-arduino/10-arduclema-atmega328.html)

Arduino Screwshield (http://www.bricogeek.com/shop/287-arduino-screwshield.html)

Interruptor Reed blindado

Caja para Arduino (http://www.bricogeek.com/shop/arduino/289-caja-para-arduino.html)

LCD (librerías Arduino):

LCDS

enlace 1 (http://www.bricogeek.com/shop/pantallas-lcd-oled/27-pantalla-lcd-16x2-caracteres-fstn-blanco-sobre-negro.html),

Librerías:

LiquidCrystal (http://arduino.cc/es/Tutorial/LiquidCrystal)

New LiquidCrystal https://bitbucket.org/fmalpartida/new-liquidcrystal/wiki/Home

para controlar este display http://es.aliexpress.com/item/New-2004-204-20X4-Character-LCD-Module-Display-For-Arduino-Serial-IIC-I2C-TWI-DROP-SHIPPING/1019278159.html

Módulos conectar y listo

Electan:

http://www.electan.com/mobile_product_info.php?cPath=345&products_id=3043

http://www.electan.com/mobile_product_info.php?cPath=345&products_id=2999

Compra Dx.com

Thursday, 12 December 2013 17:35 | Home (http://www.dx.com/)| Help (http://help.dx.com/)

Dear Pedro,

Order No.: 131212001041392787 (https://my.dx.com/MyOrders/OrderDetail/131212001041392787) | Order Date: Thursday, 12 December 2013 17:35

Thank you for ordering from DX.com.

Your order has been successfully created and the transaction is being processed.

If the payment for your order was processed successfully, you can check your order status by clicking My Orders (https://my.dx.com/MyOrders/Index) from your DX account.

You will receive a notification email from us once your transaction is confirmed.

Please confirm your order details and shipping address as below:

Item(s) | Purchase Price | Discount | Gift Qty | Qty | LineTotalPrice
LCD Keypad Shield for Arduino Duemilanove & LCD 1602 (Works with Official Arduino Boards)-118059 (http://www.dx.com/p/118059) | US$ 6.40 | US$ 0.00 | 0 | 1 | US$ 6.40
1602A 16 x 2 Lines White Character LCD Module w/ Blue Backlight (DC 5V)-151978 (http://www.dx.com/p/151978) | US$ 3.50 | US$ 0.00 | 0 | 1 | US$ 3.50
Sensor Shield V4.0 for Arduino (Works with Official Arduino Boards)-66849 (http://www.dx.com/p/66849) | US$ 4.70 | US$ 0.00 | 0 | 1 | US$ 4.70
Hall Magnetic Sensor / Switch Module for Smart Car-141363 (http://www.dx.com/p/141363) | US$ 6.10 | US$ 0.00 | 0 | 1 | US$ 6.10
Breadboard Jumper Wires for Electronic DIY (70-Cable Pack)-80208 (http://www.dx.com/p/80208) | US$ 3.17 | US$ 0.00 | 0 | 1 | US$ 3.17

| | GoodsTotal: | US$23.87
ShippingFee Discount: | US$1.70 | ShippingFee: | US$0.00
| | TotalAmount: | US$25.57
Grand Total: US$23.87

Otras webs

http://tallerarduino.com

http://arduinolab.wordpress.com/

http://forum.arduino.cc/index.php?topic=68353.5;wap2 Problema con velocímetro

Quizá esto sirva de ayuda para el truncamiento: http://forum.arduino.cc/index.php?topic=208565.0

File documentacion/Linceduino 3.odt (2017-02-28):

Pedro escribe en azul

Linceduino 2

Especificaciones

Tras conversación telefónica con Manuel Barbero, me comenta las siguientes especificaciones que serían las ideales para un nuevo linceduino.

- El sistema de medición a través de pulsos magnéticos es mucho más preciso que un sistema gps y por tanto el funcionamiento y cálculos por paso de sensor magnético son prioritarios. Se mantiene el sistema de medición magnética de linceduino 1.
- Sería muy importante que los datos que recoge magnéticamente linceduino a través del sistema magnético que se trasladarán en tiempo real a un portátil, tablet o smartphone a través de gprs u otro método, por tanto, es necesario un módulo gprs u otro sistema de transmisión de datos a distancia. Habría que estudiar las incompatibilidades de los módulos sd (presente en linceduino 1) y el módulo gprs sobre todo coincidencias de pines, estas coincidencias también hay que estudiarlas con respecto a los módulos lcd (lcd keypad shield en el caso de linceduino 1) u otro lcd. En caso de incompatibilidades se podría prescindir del módulo sd si se transmiten los datos de forma correcta mediante gprs.
- También sería conveniente un módulo gps para transmitir la posición aproximada del vehículo en tiempo real, y realizar un seguimiento del posicionamiento de vehículo en tiempo real.
- Habría que separar físicamente los módulos de Arduino del lcd, uniéndolos mediante cableado, de manera que el lcd ocupe un lugar en la zona de visión del conductor y el resto de módulos se ubiquen en un lugar intermedio entre el display y el sensor magnético, protegido frente a vibraciones.
- En el caso de mantener el módulo de tarjeta SD, habrá que posicionarlo de manera que se pueda introducir y extraer la tarjeta SD sin tener que manipular el resto de módulos.
- Mejorar (si se puede) la seguridad de las uniones entre los cables y los módulos de Arduino, para evitar que, por vibraciones, se puedan soltar o realizar falsos contactos. Para esto he pensado en este producto shield de clemas http://www.cooking-hacks.com/shop/arduino/shields/screw-shield-for-arduino o mejor este http://www.cooking-hacks.com/proto-screw-shield-assembled-arduino-compatible o este http://www.cooking-hacks.com/screw-shield-for-arduino

Materiales

Emisor y receptor tipo 3DR Robotics

http://www.amazon.es/gp/product/B00L10R3MG?psc=1&redirect=true&ref_=oh_aui_detailpage_o02_s00

Lcd I2C

http://www.amazon.es/gp/product/B00Q6WQAAK?psc=1&redirect=true&ref_=oh_aui_detailpage_o05_s00

Screw Shiled (Clemas para arduino) http://www.amazon.es/gp/product/B00Q6WL31G?psc=1&redirect=true&ref_=oh_aui_detailpage_o00_s00

Enviando y recibiendo datos por radiofrecuencia

Vídeo de como hacerlo: https://www.youtube.com/watch?v=CEOZVB9U204

Investigación:

Como conectar LCD a arduino pero no en un shield:

http://arduino-info.wikispaces.com/LCD-Blue-I2C (este es el nuestro)

https://geekytheory.com/tutorial-arduino-conectar-lcd-16x2-por-protocolo-i2c/

http://elcajondeardu.blogspot.com.es/2013/12/tutorial-conectando-una-pantalla-lcd.html

Pines usado en los shields:

http://playground.arduino.cc/Main/ShieldPinUsage

Referencia sobre arduino Mega

http://www.arduino.cc/en/Main/arduinoBoardMega

Graficando datos con KST

http://real2electronics.blogspot.com.es/2009/11/graficar-con-kst.html

http://blog.bricogeek.com/noticias/arduino/graficando-datos-con-arduino/

Leer datos del puerto serie y processing

http://www.sistemasorp.es/2010/11/09/processing-y-el-puerto-serie/

Nos queda por trabajar:

1. Trabajar sobre el nuevo lcd, adaptando el programa del año pasado.
2. Fijación de cables con clemas.
3. Adaptar el software a la transmisión de datos y mejorar el software del año pasado.
4. Comprobar el alcance de la señal.
5. Comprobar los fallos en la emisión de señales.
6. Comprobar consumo de batería.

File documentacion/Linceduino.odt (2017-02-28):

AYUDA ELECTRÓNICA PARA LINCE CON ARDUINO. LINCEDUINO.

Hardware definitivo


Descripción de conexionados

Pulsador NA de Marcha de motor: una pata a 5V, otra a pin 19 y resistencia 10 K y de resistencia de 10K a GND.

Pulsador NA de Paro de motor: una pata a 5V, otra a pin 18 y resistencia 10 K y de resistencia de 10K a GND.

Sensor Hall: cable marrón a 5V, cable azul a GND y cable negro a pin 21.

Software definitivo V 1.1

Código nuevo (con botonera para controlar guardado)

#include <LiquidCrystal.h>

#include <math.h>

#include <SD.h>

#define REFRESCO_SD 4 //Frecuencia de guardado

#define CS 4 // pin que marca el fabricante de SD Shield

LiquidCrystal lcd(8, 9, 4, 5, 6, 7);

float radio=236.82; // radio de la rueda en mm hay que poner la real del lince

volatile float tiempopaso, tiempovuelta;//tiempo (hasta la activación del sensor y de una vuelta)

volatile float velocidad, velocidadm; //velocidades (instantánea y media)

volatile float distancia; //distancia recorrida desde que empieza a circular

volatile int lineasBuffer = 0; // lineas de buffer guardadas

volatile int nvueltas = 0; //vuelta de rueda

volatile int marcha,paro;// estado de pulsadores de impulso o paro

String minutos, segundos; //minutos y segundos desde el inicio

char s_string [10];

char m_string [10];

unsigned long tiempo1=0; //tiempo inicial

int vueltas; //vuelta del circuito

String buffer=""; // Almacenamiento temporal de datos recogidos de ISR, para la tarjeta SD

volatile int botonpulsado=0;// Botón del lcdkeypad

File dataFile; //Fichero para guardar datos

bool c = true; //Booleano para la representación

void setup() {

attachInterrupt(2, calculos, RISING);//pin de interrupción 21 arduino mega para sensor hall

attachInterrupt(4, calculosmarcha, RISING);//pin de interrupción 19 arduino mega: marcha

attachInterrupt(5, calculosparo, RISING);//pin de interrupción 18 arduino mega: paro

lcd.begin(16, 2); //iniciamos la pantalla lcd

pinMode(CS, OUTPUT);

SD.begin(CS);//inicializa la SD (tiene que estar insertada) sólo lo hace una vez

}

void calculos() {

//Calcula los datos a representar

//if (nvueltas==1) {tiempo1=millis();}

nvueltas++;

tiempovuelta=millis()-tiempopaso;//tiempo por vuelta

tiempopaso=millis();//tiempo desde que se produjo la interrupcion

velocidad=(TWO_PI*radio*3.6)/tiempovuelta; // (km/h), [mm/ms*3,6 para pasar a km/h]

distancia=(nvueltas*TWO_PI*radio)/1000000; //distancia total (km)

vueltas= int((distancia)/1.626)+1; // el circuito tiene 1626 m= 1.626 Km

//solo guarda en buffer y por tanto guarda en fichero cuando si se ha pulsado el boton select

guardabuffer();

}

void calculosmarcha() {

//Interrupción para pulsador 'marcha'

marcha=1;

guardabuffer();

}

void calculosparo() {

//Interrupción para pulsador 'paro'

paro=1;

guardabuffer();

}

void guardabuffer(){

//Guarda los datos temporalmente en un buffer

if(botonpulsado==5) {

buffer += String(int((millis()-tiempo1)/1000));buffer += ";";

buffer += nf(velocidad,2,2);buffer += ";";

buffer += nf(velocidadm,2,2);buffer += ";";

buffer += nf(distancia,2,2);buffer += ";";

buffer += vueltas;buffer += ";";

buffer += marcha;buffer += ";";

buffer +=paro; buffer += "\n";

lineasBuffer++;

}

}

void guardadatos(){

//Guarda el buffer en un archivo

dataFile = SD.open("tele.txt", FILE_WRITE);

dataFile.print(buffer);

lineasBuffer = 0;

buffer = "";

dataFile.close();

lcd.setCursor(15,1);

c = !c;

if(c) {lcd.print("|");}

else {lcd.print("-");}

}

String nf(float n, int cifras, int decimales) {

char numero [10];

dtostrf(n,(cifras+decimales+1),decimales,numero);

int punto = String(numero).indexOf(".");

String parte_entera = String(numero).substring(0,punto);

String parte_decimal = String(numero).substring(punto+1);

return parte_entera + "," + parte_decimal;

}

String tiempo() {

// Devuelve el tiempo de la forma ‘000:00’

dtostrf((millis()-tiempo1)/60000,3,0,m_string);

dtostrf(((millis()-tiempo1) % 60000)/1000,1,0,s_string);

minutos = String(m_string);

segundos = String(s_string);

if (segundos.length() < 2) {segundos = "0" + segundos;}

return minutos + ":" + segundos;

}

void leebotones (int valorsensor) {

// A cada botón le corresponde un rango de valores

if (valorsensor <1000 || valorsensor>1100) {botonpulsado=0;} //ningun boton pulsado

if (valorsensor<10) { botonpulsado=1;}

if (valorsensor>90 && valorsensor<110) {botonpulsado=2;}

if (valorsensor>200 && valorsensor<300) {botonpulsado=3;}

if (valorsensor>400 && valorsensor<450) {botonpulsado=4;}

if (valorsensor>600 && valorsensor<650) {botonpulsado=5;SD.begin(CS);} //boton select

}

void loop() {

//Bucle principal. Representa y reinicia variables

leebotones(analogRead(0)); //comprueba que botón ha sido pulsado o sino se ha pulsado (0)

if (nvueltas==1) {tiempo1=millis();}

if (lineasBuffer >= REFRESCO_SD) {guardadatos();}

velocidadm=(TWO_PI*radio*3.6*nvueltas)/(millis() - tiempo1);

lcd.setCursor(0,0);

if((millis()-tiempopaso) < 3000) {if (velocidad<100) {lcd.print(nf(velocidad,2,1));}} //si la velocidad es > 100 no representa}

else {lcd.print(" 0,0");}

lcd.setCursor(5,0);

if (velocidadm<100) {lcd.print(nf(velocidadm,2,1));}

lcd.setCursor(15,0);

if (botonpulsado==5) {lcd.print("G");}

else {lcd.print("N");}

//lcd.setCursor(14,0);

//lcd.print(marcha);

//lcd.setCursor(15,0);

//lcd.print(paro);

lcd.setCursor(10,0);

if (vueltas<=9) {

lcd.print("V:");

lcd.print(vueltas);}

else {lcd.print("FINAL");}

lcd.setCursor(0,1);

lcd.print(nf(distancia,3,2));

lcd.setCursor(7,1);

lcd.print(tiempo());

lcd.setCursor(14,1);

if(velocidad>100 || velocidadm>100 ){lcd.print("E");}

else{lcd.print(" ");}

marcha=0;

paro=0;

delay(200);

}

MANUAL PARA LINCEDUINO

- Cuando se inicia (reset o alimentación) cuenta el tiempo. Lo reinicia cuando se mueve.
- Para grabar datos hay que darle al botón “select”. Para que deje de grabar datos hay que pulsar cualquier botón que no sea “select” o “reset” (se puede hacer en box). Es conveniente hacerlo con el vehículo parado, para asegurar el cierre del fichero de datos.
- Antes de la carrera:
  - La persona que pilota pulsa reset (reinicio del tiempo) y luego select (grabación).
  - Linceduino empezará a grabar con un tiempo inicial (desde el reinicio hasta empezar a moverse) que hay que quitar de los tiempos grabados.
- LCD (Pantalla) de Linceduino

1ª Fila

V. Instantánea [km/h] 00,0 (2 enteros 1 decimal) | V. Media [km/h] 00,0 (2 enteros 1 decimal) | Nº de vuelta (V:0) En la vuelta final pone FINAL | Grabación (último) N: grabado inactivo G: grabado activo

2ª Fila

Distancia [km] 000,00 (3 enteros 2 decimales) | Tiempo [min:s] 000,00 (3 enteros 2 decimales) | Error de sensor (penúltimo) E: error del sensor [Blanco]: sin error | Animación de grabación (último) [Animación]: graba

HOJA DE CÁLCULO

Archivo TELE.TXT vinculado a hoja de cálculo de datos, hay otra hoja de gráfico y otra de cabeceras del gráfico.

AYUDAS E INVESTIGACIONES

Ideas de Daniel Segura (Ingeniero Informático) sobre buffer y nuestro programa no hay nada metido en el programa

1) Las ISR (rutinas de tratamiento de interrupciones) (calculos() en el codigo) han de ser de codigo muy ligeras, la que se está usando es muy lenta, ya que dentro de la ISR hasta se graba en la tarjeta SD , haciendo una llamada a otra subrutina "guardadatos()".

2) Las variables globales que vayan a ser actualizadas dentro de una ISR deben ser declaradas como "volatile", para garantizar que se actualizan correctamente.

En palabras de los tipos de Arduino:

"About Interrupt Service Routines

ISRs are special kinds of functions that have some unique limitations most other functions do not have. An ISR cannot have any parameters, and they

shouldn't return anything.

Generally, an ISR should be as short and fast as possible. If your sketch uses multiple ISRs, only one can run at a time, other interrupts will be ignored (turned off) until the current one is finished. as delay() and millis() both rely on interrupts, they will not work while an ISR is running.

delayMicroseconds(), which does not rely on interrupts, will work as expected.

Typically global variables are used to pass data between an ISR and the main program. To make sure variables used in an ISR are updated correctly, declare them as volatile. "

Bien, como te dije a mi eso de escribir en SD tol rato pos como que no me gustaba un pelo, mejor ir acumulando informacion en memoria (buffer) y volcar a SD cuando el buffer se llene. Dicho buffer lo hemos tirado a lo mas sencillo posible, es un String al que se van encadenando los valores recogidos en "calculos()" añadiendo al final de cada secuencia un salto de linea.

La constante REFRESCO_SD (#define REFRESCO_SD 2) indica el tamaño del buffer en líneas, cuando se llene, entonces dentro de loop() y no en la ISR se llamará a la función de "guardaDatos()", que se encargará en un solo paso de volcar toda la informacion a la SD.

OJO: puedes jugar con la variable REFRESCO_SD (para minimizar el numero de volcados a SD) aumentando su valor, pero arduino solo escribe realmente en la SD cuando se cierra el fichero, que en el código se produce cuando se llena el buffer, asi que no pongas un buffer muy grande, porque o bien te quedarás sin memoria ó sin que se haya terminado de rellenar el buffer y no se vuelque a la SD. Yo lo he dejado en cada par de vueltas, lo realmente interesante es que hemos sacado del codigo de la ISR la grabacion de datos a la SD.

La digestión del programa sería tal que así:

Las llamadas a la ISR calculos() lanzan un guardado de los datos al buffer (hemos creado una funcion guardabuffer() a tal efecto), esto es, graba a memoria y no en la SD

// La ISR llama a guardabuffer();

void calculos() {

nvueltas++;

vueltas=(distancia)/1.626; // el circuito tiene 1626 m= 1.626 Km

guardabuffer(); //Actualiza el buffer (en memoria, no en SD)

}

// guardabuffer actualiza la variable global buffer encadenandole los valores al final

void guardabuffer(){

buffer += nf(velocidad,2,2);buffer += ",";

buffer += nf(velocidadm,2,2);buffer += ",";

buffer += nf(distancia,2,2);buffer += ",";

buffer += nf(((millis()-tiempo1)/1000),2,2);buffer += "\n";

lineasBuffer++; // variable de control de tamaño del buffer

}

En el bucle principal se chequea la condicion del buffer lleno, si lo está se llama a guardadatos

void loop() {

if (nvueltas==1) {tiempo1=millis();}

//Aqui se llama a guardadatos() si el BUFFER esta lleno

if (lineasBuffer >= REFRESCO_SD) {

guardadatos();

}

guardadatos, ahora queda mucho más escueta, ya que solo tiene que guardar el buffer, que es un string engordado,

void guardadatos(){

dataFile=SD.open("tele.txt", FILE_WRITE); // Creamos archivo de texto

if(dataFile){

dataFile.print(buffer); //Almacenamos el contenido del buffer

lineasBuffer=0; //Reseteamos el numero de lineas usadas del buffer

buffer=""; // Limpiamos el buffer y a empezar de nuevo cuando se vuelva a invocar la ISR

dataFile.close(); // Cerramos la escritura dentro del archivo <- AQUI ES REALMENTE CUANDO SE GRABA LA INFORMACIÓN

Fale, esta es mas o menos la idea que tenia en mente cuando hablamos, te adjunto el codigo, que no puedo probar, pero que compilar compila :).

En principio debería ir mejor, no he tocado nada que no fueren los datos, nada de nada de la LCD y tal, porque en los manuales de arduino viene tal y como está puesta, nosotros lo haciamos en Renesas con temporizadores que lanzaban una interrupción cada determinado intervalo de tiempo y actualizabas en su ISR la pantalla y así no andabas constantemente revisando la pantalla en el bucle principal.

Ojo, los buffers de verdad son toda una infraestructura soportada por el sistema operativo (o librerias) nosotros hemos abusao del lenguaje pa hacer esto, que no es ni de coña un buffer de verdad, pero para entendernos creo q vale ¿no?.

El codigo lo llevas adjunto, o bien le puedes echar un ojo aquí (https://github.com/danudoni/algo/blob/master/algo.ino) (https://github.com/danudoni/algo/blob/master/algo.ino)

Espero haber sido de ayuda. Un abrazo

Especificaciones de Linceduino e-mails de Manuel Barbero.

Especificaciones 2

CARACTERÍSTICAS DESEABLES PARA EL SISTEMA LINCEDUINO:

- Velocidad instantánea actual en km/h

- Velocidad media en km/h

- Distancia recorrida en kilómetros medida desde la salida del Lince, con dos cifras decimales. Éste dato se puede calcular a partir de la velocidad media y el tiempo transcurrido.

- Tiempo transcurrido en minutos y segundos desde la salida del Lince.

- Indicador en el que se lea "VUELTA Nº " y a continuación 1, 2, ... hasta 9, y al llegar a la última vuelta, la número 10, cambiaría la indicación a "VUELTA FINAL". Éste dato se calcularía en función del tiempo transcurrido desde la salida y del hecho de que cada vuelta tiene una longitud de 1,63 km.

- Pulsador de Reset.

Hemos valorado todos éstos datos como muy convenientes para facilitar la función del piloto.

En el caso ideal, y en el caso de que el display fuese muy pequeño para que se mostrase simultáneamente toda ésta información, se podría considerar dos displays.

- El autoreset a los 5 segundos de inactividad, no es deseable, porque puede darse el caso (por desgracia, mas de lo deseable), de que en competición, el vehículo se pare por avería instantánea, y que vuelva a arrancar. En éste caso, el tiempo de parada cuenta para contabilizar la velocidad media. Pienso que una posible idea podría ser colocar otro pulsador de parada, que, en condiciones normales, el piloto pulsaría al cruzar la línea de meta, con lo que los datos al pulsar éste pulsador se quedarían "congelados", tanto la velocidad media, distancia, tiempo e indicación "VUELTA FINAL".

- El pulsador de reset debería resetear todo el sistema, pero no debería iniciar el contador de tiempo hasta que el vehículo no empiece a moverse. El motivo es que el coche, al estar en la línea de salida, tiene dos minutos para salir. En parte de ese tiempo, el piloto hace una checklist, pero la velocidad media y el tiempo debería comenzar a contar cuando el coche empiece a moverse.

- Los decimales, serían uno para las velocidades, dos para la distancia (en kilómetros), el tiempo en minutos y segundos.

Especificaciones 1

Te comento los datos sobre la rueda del Lince que me pediste.

Aquí tienes un enlace a una buena imagen del Lince en el que se le ve la rueda delantera izquierda. Si te fijas, a eso de las 1, usando lenguaje de los pilotos, verás en un radio el imán del medidor de velocidad de bicicleta:

http (http://2.bp.blogspot.com/-qARpL4smn-c/UbcLVnt5eVI/AAAAAAAAC6w/REsKGfDmiBA/s1600/Lince-1.jpg)://2. (http://2.bp.blogspot.com/-qARpL4smn-c/UbcLVnt5eVI/AAAAAAAAC6w/REsKGfDmiBA/s1600/Lince-1.jpg)bp (http://2.bp.blogspot.com/-qARpL4smn-c/UbcLVnt5eVI/AAAAAAAAC6w/REsKGfDmiBA/s1600/Lince-1.jpg). (http://2.bp.blogspot.com/-qARpL4smn-c/UbcLVnt5eVI/AAAAAAAAC6w/REsKGfDmiBA/s1600/Lince-1.jpg)blogspot (http://2.bp.blogspot.com/-qARpL4smn-c/UbcLVnt5eVI/AAAAAAAAC6w/REsKGfDmiBA/s1600/Lince-1.jpg). (http://2.bp.blogspot.com/-qARpL4smn-c/UbcLVnt5eVI/AAAAAAAAC6w/REsKGfDmiBA/s1600/Lince-1.jpg)com (http://2.bp.blogspot.com/-qARpL4smn-c/UbcLVnt5eVI/AAAAAAAAC6w/REsKGfDmiBA/s1600/Lince-1.jpg)/- (http://2.bp.blogspot.com/-qARpL4smn-c/UbcLVnt5eVI/AAAAAAAAC6w/REsKGfDmiBA/s1600/Lince-1.jpg)qARpL (http://2.bp.blogspot.com/-qARpL4smn-c/UbcLVnt5eVI/AAAAAAAAC6w/REsKGfDmiBA/s1600/Lince-1.jpg)4 (http://2.bp.blogspot.com/-qARpL4smn-c/UbcLVnt5eVI/AAAAAAAAC6w/REsKGfDmiBA/s1600/Lince-1.jpg)smn (http://2.bp.blogspot.com/-qARpL4smn-c/UbcLVnt5eVI/AAAAAAAAC6w/REsKGfDmiBA/s1600/Lince-1.jpg)- (http://2.bp.blogspot.com/-qARpL4smn-c/UbcLVnt5eVI/AAAAAAAAC6w/REsKGfDmiBA/s1600/Lince-1.jpg)c (http://2.bp.blogspot.com/-qARpL4smn-c/UbcLVnt5eVI/AAAAAAAAC6w/REsKGfDmiBA/s1600/Lince-1.jpg)/ (http://2.bp.blogspot.com/-qARpL4smn-c/UbcLVnt5eVI/AAAAAAAAC6w/REsKGfDmiBA/s1600/Lince-1.jpg)UbcLVnt (http://2.bp.blogspot.com/-qARpL4smn-c/UbcLVnt5eVI/AAAAAAAAC6w/REsKGfDmiBA/s1600/Lince-1.jpg)5 (http://2.bp.blogspot.com/-qARpL4smn-c/UbcLVnt5eVI/AAAAAAAAC6w/REsKGfDmiBA/s1600/Lince-1.jpg)eVI (http://2.bp.blogspot.com/-qARpL4smn-c/UbcLVnt5eVI/AAAAAAAAC6w/REsKGfDmiBA/s1600/Lince-1.jpg)/ (http://2.bp.blogspot.com/-qARpL4smn-c/UbcLVnt5eVI/AAAAAAAAC6w/REsKGfDmiBA/s1600/Lince-1.jpg)AAAAAAAAC (http://2.bp.blogspot.com/-qARpL4smn-c/UbcLVnt5eVI/AAAAAAAAC6w/REsKGfDmiBA/s1600/Lince-1.jpg)6 (http://2.bp.blogspot.com/-qARpL4smn-c/UbcLVnt5eVI/AAAAAAAAC6w/REsKGfDmiBA/s1600/Lince-1.jpg)w (http://2.bp.blogspot.com/-qARpL4smn-c/UbcLVnt5eVI/AAAAAAAAC6w/REsKGfDmiBA/s1600/Lince-1.jpg)/ (http://2.bp.blogspot.com/-qARpL4smn-c/UbcLVnt5eVI/AAAAAAAAC6w/REsKGfDmiBA/s1600/Lince-1.jpg)REsKGfDmiBA (http://2.bp.blogspot.com/-qARpL4smn-c/UbcLVnt5eVI/AAAAAAAAC6w/REsKGfDmiBA/s1600/Lince-1.jpg)/ (http://2.bp.blogspot.com/-qARpL4smn-c/UbcLVnt5eVI/AAAAAAAAC6w/REsKGfDmiBA/s1600/Lince-1.jpg)s (http://2.bp.blogspot.com/-qARpL4smn-c/UbcLVnt5eVI/AAAAAAAAC6w/REsKGfDmiBA/s1600/Lince-1.jpg)1600/ (http://2.bp.blogspot.com/-qARpL4smn-c/UbcLVnt5eVI/AAAAAAAAC6w/REsKGfDmiBA/s1600/Lince-1.jpg)Lince (http://2.bp.blogspot.com/-qARpL4smn-c/UbcLVnt5eVI/AAAAAAAAC6w/REsKGfDmiBA/s1600/Lince-1.jpg)-1. (http://2.bp.blogspot.com/-qARpL4smn-c/UbcLVnt5eVI/AAAAAAAAC6w/REsKGfDmiBA/s1600/Lince-1.jpg)jpg (http://2.bp.blogspot.com/-qARpL4smn-c/UbcLVnt5eVI/AAAAAAAAC6w/REsKGfDmiBA/s1600/Lince-1.jpg)


La llanta es de 16 pulgadas (40,64 cm de diámetro). La rueda totalmente montada con el neumático, y con una presión de 6kg/cm2, tiene un desarrollo de 1,498 m.

Éste desarrollo puede variar con la presión de inflado y con el peso total coche-piloto. Ante ésta variabilidad, yo te pediría, si fuese posible, que el programa pudiese preguntar y guardar en memoria el desarrollo real en cada momento, en cada configuración.

Una cuestión que me preocupa es el tiempo de respuesta del medidor de velocidad, es decir, que ante una velocidad estable, cuando ésta cambia, cuánto tiempo necesita el medidor para mostrar la nueva velocidad. Nuestro límite está en el tiempo de respuesta de los medidores de velocidad de bicicleta, que tienen un tiempo de 3 segundos (ésto es demasiado para nuestras necesidades). Por lo que sería necesario cuantificarlo en el ARDUINO.

Al depender el tiempo de respuesta del tiempo por revolución de la rueda junto con otros parámetros debidos al hardware del sistema y al software del mismo, nosotros intentamos bajar el tiempo de respuesta del medidor de bicicleta aumentando el número de imanes instalados en la rueda. Llegamos a pensar en poner 10, con lo que la indicación de la velocidad del medidor, para 25km/h reales hubiese sido 250km/h, con lo que el piloto lo único que debería imaginarse es la coma. No pudimos hacerlo, porque habría que variar el desarrollo introducido en el medidor, y los límites que traen esos aparatos no nos dejaban poner el desarrollo resultante. Lo digo por si al medir el tiempo de respuesta, si éste fuese alto, siempre se podría poner no un imán, sino dos o tres. En fin, son solo ideas fruto de nuestra experiencia, por si os valen.

Es importante que el sistema disponga de un pulsador que el piloto pueda pulsar cuando el vehículo esté parado en la línea de salida, para resetear la velocidad media y que comience a mostrar los parámetros de velocidad instantánea y media al comenzar a moverse.

Pruebas con reed en la Red

ver video http (http://www.youtube.com/watch?v=KNSgAHnP2wM):// (http://www.youtube.com/watch?v=KNSgAHnP2wM)www (http://www.youtube.com/watch?v=KNSgAHnP2wM). (http://www.youtube.com/watch?v=KNSgAHnP2wM)youtube (http://www.youtube.com/watch?v=KNSgAHnP2wM). (http://www.youtube.com/watch?v=KNSgAHnP2wM)com (http://www.youtube.com/watch?v=KNSgAHnP2wM)/ (http://www.youtube.com/watch?v=KNSgAHnP2wM)watch (http://www.youtube.com/watch?v=KNSgAHnP2wM)? (http://www.youtube.com/watch?v=KNSgAHnP2wM)v (http://www.youtube.com/watch?v=KNSgAHnP2wM)= (http://www.youtube.com/watch?v=KNSgAHnP2wM)KNSgAHnP (http://www.youtube.com/watch?v=KNSgAHnP2wM)2 (http://www.youtube.com/watch?v=KNSgAHnP2wM)wM (http://www.youtube.com/watch?v=KNSgAHnP2wM)

Nuestras Pruebas e Implementaciones para el Cálculo de Velocidad Media e Instántánea

La Lorenzina.

Horquilla portátil para realizar pruebas de ruedas. By Lorenzo Olmo.

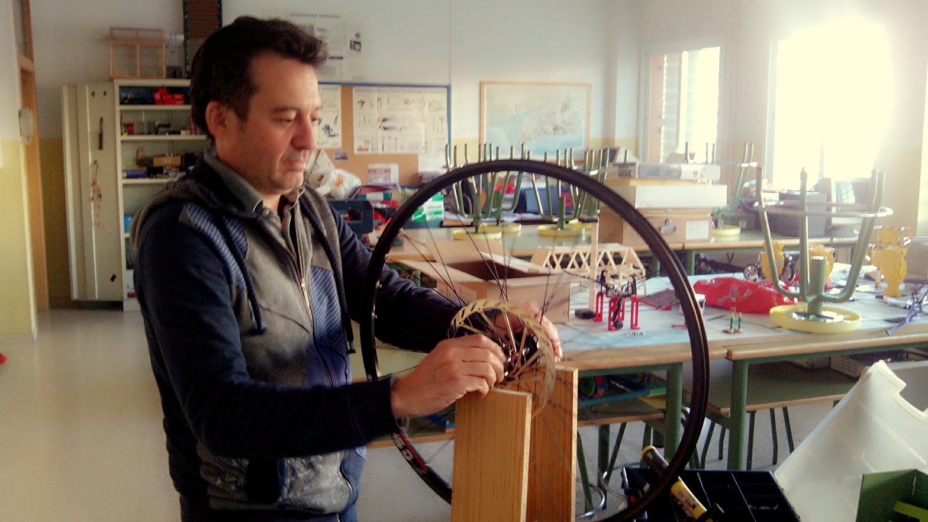
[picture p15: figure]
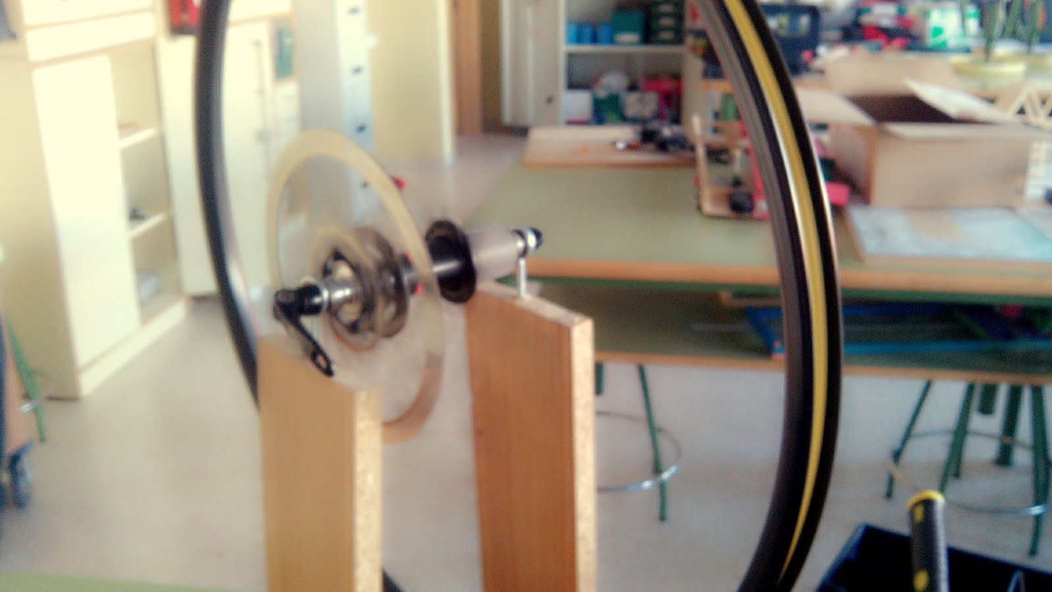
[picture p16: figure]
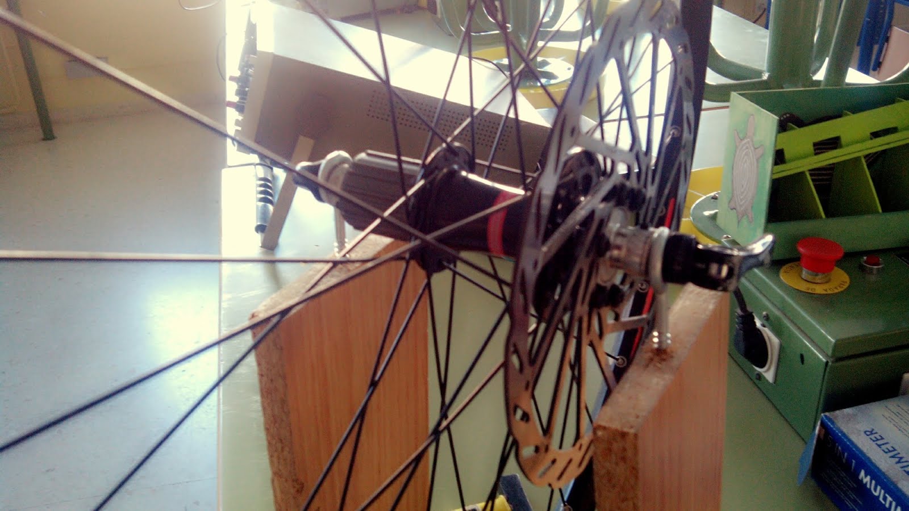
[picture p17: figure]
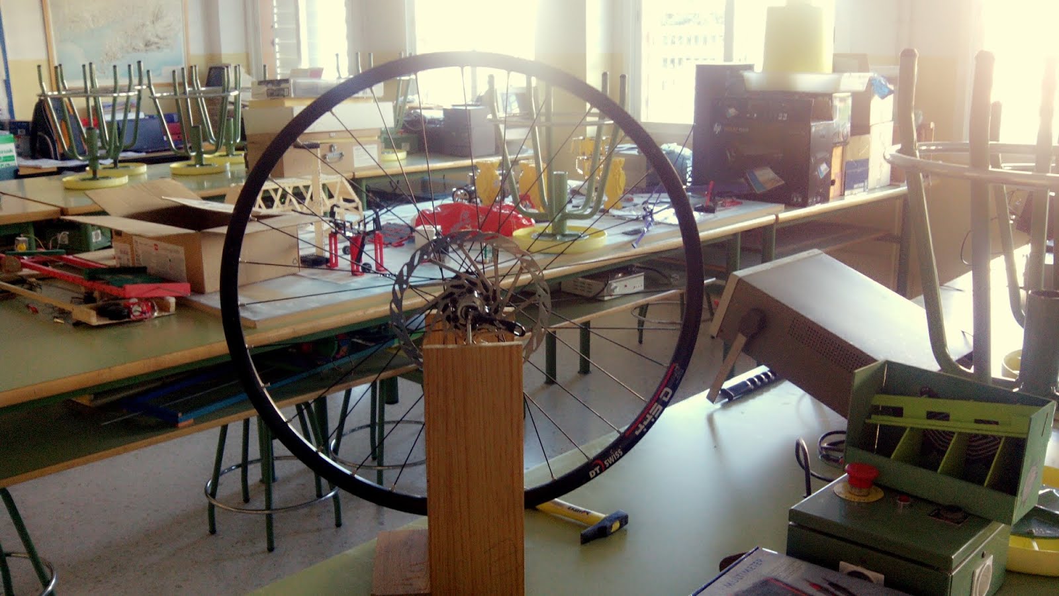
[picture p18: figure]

Programación

Ideas:

Podemos usar un sólo imán y sabiendo el desarrollo de la rueda y el tiempo por vuelta lo tenemos todo. El usar un sólo imán es por reducir errores de cálculo a la hora de colocar más imanes.

En realidad estamos usando un sensor Hall, que cuando está un campo magnético cerca de él (<10 mm) genera una señal eléctrica en el pin de 0.

Velocidades media e instantánea con LCD

/Incluimos la librería de LCD que trae arduino

#include <LiquidCrystal.h>

//Indicamos los pins que vamos a usar para

//comunicarnos con la pantalla

//En mi caso, al usar una lcd shield los botones

//son los siguientes

LiquidCrystal lcd(8, 9, 4, 5, 6, 7);

//Creamos una constante para tomar

//indicar a que pin está conectado

//const int sensoranalogico = 0;

//Creamos una variable para almacenar los

//valores tomados por los botones

int valorsensor = 0;

unsigned long tiempototal;

unsigned long tiempoparcial;

int vuelta=1498;//mm por vuelta

float velocidadactual;

float velocidadmedia;

int nvueltas = 0;

int pin=52;

//Inicia el void setup que solo se ejecuta

//una vez

void setup() {

//iniciamos la pantalla lcd y le

//indicamos el número de columnas x el número de filas

lcd.begin(16, 2);

pinMode (pin,INPUT);//pone de entrada el pin 52

}

//Inicia el loop que se ejecutará

//mientras el arduino esté conectado

void loop() {

velocimetro();

}

void velocimetro(){

tiempototal=millis();

tiempoparcial=(pulseIn (pin,LOW))/1000;//ms por vuelta

velocidadactual=(vuelta/tiempoparcial)*3.6;// vel. instantanea

if(tiempoparcial!=0){nvueltas = nvueltas+1;}

velocidadmedia = (nvueltas*vuelta*3.6)/tiempototal;

lcd.setCursor(0,0);

lcd.print("Vel.Inst: ");

lcd.print (velocidadactual);

lcd.setCursor(0,1);

lcd.print("Vel.Med: ");

lcd.print (velocidadmedia);

}

Velocidades media e instantánea segunda implementación

unsigned long tiempototal;

unsigned long tiempoparcial;

int vuelta=1498;//mm por vuelta

float velocidadactual;

float velocidadmedia;

int nvueltas = 0;

int pin=7;

void setup () {

Serial.begin(9600);

pinMode (pin,INPUT);

}

void monitoriza () {

//Serial.print ("Tiempo total (s):...");

//Serial.println (tiempototal);

//Serial.print ("Tiempo parcial (s):...");

//Serial.println (tiempoparcial);

Serial.print ("Vel. Ins (km/h):");

Serial.println (velocidadactual);

Serial.print ("Vel. Med (km/h):");

Serial.println (velocidadmedia);

//delay (1000);

}

void loop () {

tiempototal=millis();

tiempoparcial=(pulseIn (pin,LOW))/1000;//ms por vuelta

velocidadactual=(vuelta/tiempoparcial)*3.6;// vel. instantanea

if(tiempoparcial!=0){nvueltas = nvueltas+1;}

velocidadmedia = (nvueltas*vuelta*3.6)/tiempototal;

monitoriza();

}

Velocidades media e instantánea primera implementación

unsigned long tiempototal;

unsigned long tiempoparcial;

float cuartovuelta=70.686;//mm por 1/4 de vuelta en un disco de 9cm de diam.

float velocidadactual;

float velocidadmedia;

int ncuartos = 0;

int pin=7;

void setup () {

Serial.begin(9600);

pinMode (pin,INPUT);

}

void monitoriza () {

//Serial.print ("Tiempo total (s):...");

//Serial.println (tiempototal);

//Serial.print ("Tiempo parcial (s):...");

//Serial.println (tiempoparcial);

Serial.print ("Vel. Ins (km/h):");

Serial.println (velocidadactual);

Serial.print ("Vel. Med (km/h):");

Serial.println (velocidadmedia);

//delay (1000);

}

void loop () {

tiempototal=millis();

tiempoparcial=(pulseIn (pin,LOW))/1000;//ms por 1/4 de vuelta

velocidadactual=(cuartovuelta/tiempoparcial)*3.6;// vel. instantanea

if(tiempoparcial!=0){ncuartos = ncuartos+1;}

velocidadmedia = (ncuartos*cuartovuelta*3.6)/tiempototal;

monitoriza();

}

Órdenes usadas:

millis()

Descripción:

Devuelve el tiempo en milisegundos transcurridos desde que se arranco la placa Arduino con el programa actual. Este número de desbordará (volverá a cero), despues de aproximadamente 50 días.

Devuelve:

Tiempo en milisegundos desde que el programa se inició (long sin signo (unsigned long))

Ejemplo:

unsigned long time;

void setup(){
Serial.begin(9600);
}
void loop(){
Serial.print("Tiempo: ");
time = millis();
//Imprime el tiempo desde que se inició el programa
Serial.println(time);
// espera un segundo para no enviar demasiados datos
delay(1000);
}

Consejo:

Ten en cuenta que el parametro que devuelve millis() es un long sin signo por lo que pueden producirse errores si el programador intenta llevar a cabo operaciones matemáticas con otros tipos de dato como enteros.

pulseIn()

Descripción:

Lee un pulso (ya sea HIGH —alto— o LOW —bajo—) en un pin. Por ejemplo, si value es HIGH, pulseIn() espera a que el pin sea HIGH, empieza a cronometrar, espera a que el pin sea LOW y entonces detiene la medida de tiempo. Devuelve la anchura del pulso en microsegundos. Interrumpe la medida y devuelve 0 si el pulso no ha comenzado en un tiempo especificado.

La medida del tiempo en esta función ha sido determinada de forma empírica y está sujeta a errores en pulsos largos. Funciona correctamente en pulsos con una anchura de 10 microsegundos a tres minutos.

Sintaxis:

pulseIn(pin, value)

pulseIn(pin, value, timeout)

Parámetros:

pin: el número del pin en el que se realiza la medida del pulso. (int)

value: tipo de pulso. Puede ser HIGH (http://arduino.cc/es/Reference/Constants) o LOW (http://arduino.cc/es/Reference/Constants). (int)

timeout (opcional): el tiempo en microsegundos máximo a esperar antes de que se inicie el pulso. (unsigned long)

Devuelve:

el ancho del pulso (en microsegundos) ó 0 si el pulso no ha empezado antes del timeout (unsigned long)

Ejemplo

int pin = 7;
unsigned long duracion;

void setup()
{
pinMode(pin, INPUT);
}

void loop()
{
duracion = pulseIn(pin, HIGH);
}

unsigned long

Descripción:

Las variable long sin firmar (unsigned long) son variables extendidas para almacenar números, y almacenar 32 bits (4 bytes). Por el contrario que las variables long estándar, las unsigned long no almacenan números negativos, haciendo que su rango sea de 0 a 4,294,967,295 (2^32 - 1).

Ejemplo:

unsigned long tiempo;

void setup()
{
Serial.begin(9600);
}

void loop()
{
Serial.print("Tiempo: ");
tiempo = millis();
//imprime el tiempo desde el inicio del programa
Serial.println(tiempo);
// espera un segundo para no enviar cantidade masivas de datos
delay(1000);
}

Sintáxis:

unsigned long var = val;

var - el nombre de tu variable long

val - el valor que asignas a tu variable long

Ver también:

byte (http://arduino.cc/es/Reference/Byte)

int (http://arduino.cc/es/Reference/Int)

unsigned (http://arduino.cc/es/Reference/UnsignedInt) (http://arduino.cc/es/Reference/UnsignedInt)int (http://arduino.cc/es/Reference/UnsignedInt)

long (http://arduino.cc/es/Reference/Long)

Variable (http://arduino.cc/en/Reference/VariableDeclaration) (http://arduino.cc/en/Reference/VariableDeclaration)Declaration (http://arduino.cc/en/Reference/VariableDeclaration)

LCD y Arduino

Se trata de mostrar en un LCD 16x2 (16 caracteres y 2 filas) la velocidad instantanea y la media del LINCE.

Lcd 16x2 sin shield

http (http://www.proyectosarduino.com.ar/conectando-una-pantalla-lcd-a-arduino/):// (http://www.proyectosarduino.com.ar/conectando-una-pantalla-lcd-a-arduino/)www (http://www.proyectosarduino.com.ar/conectando-una-pantalla-lcd-a-arduino/). (http://www.proyectosarduino.com.ar/conectando-una-pantalla-lcd-a-arduino/)proyectosarduino (http://www.proyectosarduino.com.ar/conectando-una-pantalla-lcd-a-arduino/). (http://www.proyectosarduino.com.ar/conectando-una-pantalla-lcd-a-arduino/)com (http://www.proyectosarduino.com.ar/conectando-una-pantalla-lcd-a-arduino/). (http://www.proyectosarduino.com.ar/conectando-una-pantalla-lcd-a-arduino/)ar (http://www.proyectosarduino.com.ar/conectando-una-pantalla-lcd-a-arduino/)/ (http://www.proyectosarduino.com.ar/conectando-una-pantalla-lcd-a-arduino/)conectando (http://www.proyectosarduino.com.ar/conectando-una-pantalla-lcd-a-arduino/)- (http://www.proyectosarduino.com.ar/conectando-una-pantalla-lcd-a-arduino/)una (http://www.proyectosarduino.com.ar/conectando-una-pantalla-lcd-a-arduino/)- (http://www.proyectosarduino.com.ar/conectando-una-pantalla-lcd-a-arduino/)pantalla (http://www.proyectosarduino.com.ar/conectando-una-pantalla-lcd-a-arduino/)- (http://www.proyectosarduino.com.ar/conectando-una-pantalla-lcd-a-arduino/)lcd (http://www.proyectosarduino.com.ar/conectando-una-pantalla-lcd-a-arduino/)- (http://www.proyectosarduino.com.ar/conectando-una-pantalla-lcd-a-arduino/)a (http://www.proyectosarduino.com.ar/conectando-una-pantalla-lcd-a-arduino/)- (http://www.proyectosarduino.com.ar/conectando-una-pantalla-lcd-a-arduino/)arduino (http://www.proyectosarduino.com.ar/conectando-una-pantalla-lcd-a-arduino/)/ (http://www.proyectosarduino.com.ar/conectando-una-pantalla-lcd-a-arduino/)

LCD 16x2 key pad Shield

http (http://multitechnologyblog.wordpress.com/2012/06/15/arduino-tutorial-lcd-keypad-shield-hola-mundo-codigo/):// (http://multitechnologyblog.wordpress.com/2012/06/15/arduino-tutorial-lcd-keypad-shield-hola-mundo-codigo/)multitechnologyblog (http://multitechnologyblog.wordpress.com/2012/06/15/arduino-tutorial-lcd-keypad-shield-hola-mundo-codigo/). (http://multitechnologyblog.wordpress.com/2012/06/15/arduino-tutorial-lcd-keypad-shield-hola-mundo-codigo/)wordpress (http://multitechnologyblog.wordpress.com/2012/06/15/arduino-tutorial-lcd-keypad-shield-hola-mundo-codigo/). (http://multitechnologyblog.wordpress.com/2012/06/15/arduino-tutorial-lcd-keypad-shield-hola-mundo-codigo/)com (http://multitechnologyblog.wordpress.com/2012/06/15/arduino-tutorial-lcd-keypad-shield-hola-mundo-codigo/)/2012/06/15/ (http://multitechnologyblog.wordpress.com/2012/06/15/arduino-tutorial-lcd-keypad-shield-hola-mundo-codigo/)arduino (http://multitechnologyblog.wordpress.com/2012/06/15/arduino-tutorial-lcd-keypad-shield-hola-mundo-codigo/)- (http://multitechnologyblog.wordpress.com/2012/06/15/arduino-tutorial-lcd-keypad-shield-hola-mundo-codigo/)tutorial (http://multitechnologyblog.wordpress.com/2012/06/15/arduino-tutorial-lcd-keypad-shield-hola-mundo-codigo/)- (http://multitechnologyblog.wordpress.com/2012/06/15/arduino-tutorial-lcd-keypad-shield-hola-mundo-codigo/)lcd (http://multitechnologyblog.wordpress.com/2012/06/15/arduino-tutorial-lcd-keypad-shield-hola-mundo-codigo/)- (http://multitechnologyblog.wordpress.com/2012/06/15/arduino-tutorial-lcd-keypad-shield-hola-mundo-codigo/)keypad (http://multitechnologyblog.wordpress.com/2012/06/15/arduino-tutorial-lcd-keypad-shield-hola-mundo-codigo/)- (http://multitechnologyblog.wordpress.com/2012/06/15/arduino-tutorial-lcd-keypad-shield-hola-mundo-codigo/)shield (http://multitechnologyblog.wordpress.com/2012/06/15/arduino-tutorial-lcd-keypad-shield-hola-mundo-codigo/)- (http://multitechnologyblog.wordpress.com/2012/06/15/arduino-tutorial-lcd-keypad-shield-hola-mundo-codigo/)hola (http://multitechnologyblog.wordpress.com/2012/06/15/arduino-tutorial-lcd-keypad-shield-hola-mundo-codigo/)- (http://multitechnologyblog.wordpress.com/2012/06/15/arduino-tutorial-lcd-keypad-shield-hola-mundo-codigo/)mundo (http://multitechnologyblog.wordpress.com/2012/06/15/arduino-tutorial-lcd-keypad-shield-hola-mundo-codigo/)- (http://multitechnologyblog.wordpress.com/2012/06/15/arduino-tutorial-lcd-keypad-shield-hola-mundo-codigo/)codigo (http://multitechnologyblog.wordpress.com/2012/06/15/arduino-tutorial-lcd-keypad-shield-hola-mundo-codigo/)/ (http://multitechnologyblog.wordpress.com/2012/06/15/arduino-tutorial-lcd-keypad-shield-hola-mundo-codigo/)

http (http://www.ajpdsoft.com/modules.php?name=News&file=article&sid=627):// (http://www.ajpdsoft.com/modules.php?name=News&file=article&sid=627)www (http://www.ajpdsoft.com/modules.php?name=News&file=article&sid=627). (http://www.ajpdsoft.com/modules.php?name=News&file=article&sid=627)ajpdsoft (http://www.ajpdsoft.com/modules.php?name=News&file=article&sid=627). (http://www.ajpdsoft.com/modules.php?name=News&file=article&sid=627)com (http://www.ajpdsoft.com/modules.php?name=News&file=article&sid=627)/ (http://www.ajpdsoft.com/modules.php?name=News&file=article&sid=627)modules (http://www.ajpdsoft.com/modules.php?name=News&file=article&sid=627). (http://www.ajpdsoft.com/modules.php?name=News&file=article&sid=627)php (http://www.ajpdsoft.com/modules.php?name=News&file=article&sid=627)? (http://www.ajpdsoft.com/modules.php?name=News&file=article&sid=627)name (http://www.ajpdsoft.com/modules.php?name=News&file=article&sid=627)= (http://www.ajpdsoft.com/modules.php?name=News&file=article&sid=627)News (http://www.ajpdsoft.com/modules.php?name=News&file=article&sid=627)& (http://www.ajpdsoft.com/modules.php?name=News&file=article&sid=627)file (http://www.ajpdsoft.com/modules.php?name=News&file=article&sid=627)= (http://www.ajpdsoft.com/modules.php?name=News&file=article&sid=627)article (http://www.ajpdsoft.com/modules.php?name=News&file=article&sid=627)& (http://www.ajpdsoft.com/modules.php?name=News&file=article&sid=627)sid (http://www.ajpdsoft.com/modules.php?name=News&file=article&sid=627)=627 (http://www.ajpdsoft.com/modules.php?name=News&file=article&sid=627)

El programa siguiente está basado en la siguiente web

http (http://itmanageratschool.blogspot.com.es/2012/05/lcd-shield-with-keypad-para-arduino.html):// (http://itmanageratschool.blogspot.com.es/2012/05/lcd-shield-with-keypad-para-arduino.html)itmanageratschool (http://itmanageratschool.blogspot.com.es/2012/05/lcd-shield-with-keypad-para-arduino.html). (http://itmanageratschool.blogspot.com.es/2012/05/lcd-shield-with-keypad-para-arduino.html)blogspot (http://itmanageratschool.blogspot.com.es/2012/05/lcd-shield-with-keypad-para-arduino.html). (http://itmanageratschool.blogspot.com.es/2012/05/lcd-shield-with-keypad-para-arduino.html)com (http://itmanageratschool.blogspot.com.es/2012/05/lcd-shield-with-keypad-para-arduino.html). (http://itmanageratschool.blogspot.com.es/2012/05/lcd-shield-with-keypad-para-arduino.html)es (http://itmanageratschool.blogspot.com.es/2012/05/lcd-shield-with-keypad-para-arduino.html)/2012/05/ (http://itmanageratschool.blogspot.com.es/2012/05/lcd-shield-with-keypad-para-arduino.html)lcd (http://itmanageratschool.blogspot.com.es/2012/05/lcd-shield-with-keypad-para-arduino.html)- (http://itmanageratschool.blogspot.com.es/2012/05/lcd-shield-with-keypad-para-arduino.html)shield (http://itmanageratschool.blogspot.com.es/2012/05/lcd-shield-with-keypad-para-arduino.html)- (http://itmanageratschool.blogspot.com.es/2012/05/lcd-shield-with-keypad-para-arduino.html)with (http://itmanageratschool.blogspot.com.es/2012/05/lcd-shield-with-keypad-para-arduino.html)- (http://itmanageratschool.blogspot.com.es/2012/05/lcd-shield-with-keypad-para-arduino.html)keypad (http://itmanageratschool.blogspot.com.es/2012/05/lcd-shield-with-keypad-para-arduino.html)- (http://itmanageratschool.blogspot.com.es/2012/05/lcd-shield-with-keypad-para-arduino.html)para (http://itmanageratschool.blogspot.com.es/2012/05/lcd-shield-with-keypad-para-arduino.html)- (http://itmanageratschool.blogspot.com.es/2012/05/lcd-shield-with-keypad-para-arduino.html)arduino (http://itmanageratschool.blogspot.com.es/2012/05/lcd-shield-with-keypad-para-arduino.html). (http://itmanageratschool.blogspot.com.es/2012/05/lcd-shield-with-keypad-para-arduino.html)html (http://itmanageratschool.blogspot.com.es/2012/05/lcd-shield-with-keypad-para-arduino.html)

Programa para presentar información en la lcd keypad shield y aprovechar los botones

//Incluimos la librería de LCD que trae arduino

#include <LiquidCrystal.h>

//Indicamos los pins que vamos a usar para

//comunicarnos con la pantalla

//En mi caso, al usar una lcd shield los botones

//son los siguientes

LiquidCrystal lcd(8, 9, 4, 5, 6, 7);

//inciamos el valor del sensor analogico 0 a 0

int valorsensor = 0;

//Inicia el void setup que solo se ejecuta

//una vez

void setup() {

//iniciamos la pantalla lcd y le

//indicamos el número de columnas x el número de filas

lcd.begin(16, 2);

//Imprimimos por pantalla la frase Prueba botones

lcd.print("Prueba botones");

//Movemos el cursor a la segunda línea

lcd.setCursor(0, 2);

//Ponemos un mensaje en la segunda línea

//que nos pide que pulsemos un botón

lcd.print("Pulse un boton");

}

//Inicia el loop que se ejecutará

//mientras el arduino esté conectado

void loop() {

//Recogemos el valor en el pin analógico

//que nos dirá que botón hemos pulsado

valorsensor = analogRead(0);

//En el debuggin hemos visto que al no tener ningún botón

//pulsado los valores devueltos están entre

//1020 y 1025 por lo que cuando se den valores distintos

//a ese rango se ejecutará lo que hay dentro del if

if (valorsensor <1000 || valorsensor>1100) {

//llamamos a la función limpiar línea que veremos

//un poco más abajo

limpiarLinea();

}

if (valorsensor<10) {

lcd.setCursor(0,2);

lcd.print ("derecha");

}

if (valorsensor>90 && valorsensor<110) {

lcd.setCursor(0,2);

lcd.print ("arriba");

}

if (valorsensor>200 && valorsensor<300) {

lcd.setCursor(0,2);

lcd.print ("abajo");

}

if (valorsensor>400 && valorsensor<450) {

lcd.setCursor(0,2);

lcd.print ("izquierda");

}

if (valorsensor>600 && valorsensor<650) {

lcd.setCursor(0,2);

lcd.print ("select");

}

}

//Esta función la llamamos cuando queremos borrar

void limpiarLinea(){

//Colocamos el cursor la principio de la segunda

//línea

lcd.setCursor(0, 2);

//Con este bucle recorremos toda la línea y la ponemos

//en blanco

for (int i = 0; i < 16; i = i + 1) {

lcd.print(" ");

}

//Volvemos a colocar el cursor

//al principio de la línea

//para cuando volvamos a escribir algo

//salga desde el principio de la línea

lcd.setCursor(0, 2);

}

Trabajar con Tarjeta SD para grabar datos

Se trataría de grabar los pulsos que da el piloto para el encendido del motor y la velocidad en ese momento y el tiempo transcurrido total, todo separado por comas para ser tratado en una hoja de cálculo (documento csv) y representarse gráficamente par dar una telemetría.

http (http://tallerarduino.com/2012/11/29/arduino-tutorials-cap7-uso-de-las-memorias-sd/):// (http://tallerarduino.com/2012/11/29/arduino-tutorials-cap7-uso-de-las-memorias-sd/)tallerarduino (http://tallerarduino.com/2012/11/29/arduino-tutorials-cap7-uso-de-las-memorias-sd/). (http://tallerarduino.com/2012/11/29/arduino-tutorials-cap7-uso-de-las-memorias-sd/)com (http://tallerarduino.com/2012/11/29/arduino-tutorials-cap7-uso-de-las-memorias-sd/)/2012/11/29/ (http://tallerarduino.com/2012/11/29/arduino-tutorials-cap7-uso-de-las-memorias-sd/)arduino (http://tallerarduino.com/2012/11/29/arduino-tutorials-cap7-uso-de-las-memorias-sd/)- (http://tallerarduino.com/2012/11/29/arduino-tutorials-cap7-uso-de-las-memorias-sd/)tutorials (http://tallerarduino.com/2012/11/29/arduino-tutorials-cap7-uso-de-las-memorias-sd/)- (http://tallerarduino.com/2012/11/29/arduino-tutorials-cap7-uso-de-las-memorias-sd/)cap (http://tallerarduino.com/2012/11/29/arduino-tutorials-cap7-uso-de-las-memorias-sd/)7- (http://tallerarduino.com/2012/11/29/arduino-tutorials-cap7-uso-de-las-memorias-sd/)uso (http://tallerarduino.com/2012/11/29/arduino-tutorials-cap7-uso-de-las-memorias-sd/)- (http://tallerarduino.com/2012/11/29/arduino-tutorials-cap7-uso-de-las-memorias-sd/)de (http://tallerarduino.com/2012/11/29/arduino-tutorials-cap7-uso-de-las-memorias-sd/)- (http://tallerarduino.com/2012/11/29/arduino-tutorials-cap7-uso-de-las-memorias-sd/)las (http://tallerarduino.com/2012/11/29/arduino-tutorials-cap7-uso-de-las-memorias-sd/)- (http://tallerarduino.com/2012/11/29/arduino-tutorials-cap7-uso-de-las-memorias-sd/)memorias (http://tallerarduino.com/2012/11/29/arduino-tutorials-cap7-uso-de-las-memorias-sd/)- (http://tallerarduino.com/2012/11/29/arduino-tutorials-cap7-uso-de-las-memorias-sd/)sd (http://tallerarduino.com/2012/11/29/arduino-tutorials-cap7-uso-de-las-memorias-sd/)/ (http://tallerarduino.com/2012/11/29/arduino-tutorials-cap7-uso-de-las-memorias-sd/)

http (http://zygzax.com/2013/12/14/escribir-datos-en-una-tarjeta-sd-con-arduino-modulo-microsd-y-ethernet-shield/):// (http://zygzax.com/2013/12/14/escribir-datos-en-una-tarjeta-sd-con-arduino-modulo-microsd-y-ethernet-shield/)zygzax (http://zygzax.com/2013/12/14/escribir-datos-en-una-tarjeta-sd-con-arduino-modulo-microsd-y-ethernet-shield/). (http://zygzax.com/2013/12/14/escribir-datos-en-una-tarjeta-sd-con-arduino-modulo-microsd-y-ethernet-shield/)com (http://zygzax.com/2013/12/14/escribir-datos-en-una-tarjeta-sd-con-arduino-modulo-microsd-y-ethernet-shield/)/2013/12/14/ (http://zygzax.com/2013/12/14/escribir-datos-en-una-tarjeta-sd-con-arduino-modulo-microsd-y-ethernet-shield/)escribir (http://zygzax.com/2013/12/14/escribir-datos-en-una-tarjeta-sd-con-arduino-modulo-microsd-y-ethernet-shield/)- (http://zygzax.com/2013/12/14/escribir-datos-en-una-tarjeta-sd-con-arduino-modulo-microsd-y-ethernet-shield/)datos (http://zygzax.com/2013/12/14/escribir-datos-en-una-tarjeta-sd-con-arduino-modulo-microsd-y-ethernet-shield/)- (http://zygzax.com/2013/12/14/escribir-datos-en-una-tarjeta-sd-con-arduino-modulo-microsd-y-ethernet-shield/)en (http://zygzax.com/2013/12/14/escribir-datos-en-una-tarjeta-sd-con-arduino-modulo-microsd-y-ethernet-shield/)- (http://zygzax.com/2013/12/14/escribir-datos-en-una-tarjeta-sd-con-arduino-modulo-microsd-y-ethernet-shield/)una (http://zygzax.com/2013/12/14/escribir-datos-en-una-tarjeta-sd-con-arduino-modulo-microsd-y-ethernet-shield/)- (http://zygzax.com/2013/12/14/escribir-datos-en-una-tarjeta-sd-con-arduino-modulo-microsd-y-ethernet-shield/)tarjeta (http://zygzax.com/2013/12/14/escribir-datos-en-una-tarjeta-sd-con-arduino-modulo-microsd-y-ethernet-shield/)- (http://zygzax.com/2013/12/14/escribir-datos-en-una-tarjeta-sd-con-arduino-modulo-microsd-y-ethernet-shield/)sd (http://zygzax.com/2013/12/14/escribir-datos-en-una-tarjeta-sd-con-arduino-modulo-microsd-y-ethernet-shield/)- (http://zygzax.com/2013/12/14/escribir-datos-en-una-tarjeta-sd-con-arduino-modulo-microsd-y-ethernet-shield/)con (http://zygzax.com/2013/12/14/escribir-datos-en-una-tarjeta-sd-con-arduino-modulo-microsd-y-ethernet-shield/)- (http://zygzax.com/2013/12/14/escribir-datos-en-una-tarjeta-sd-con-arduino-modulo-microsd-y-ethernet-shield/)arduino (http://zygzax.com/2013/12/14/escribir-datos-en-una-tarjeta-sd-con-arduino-modulo-microsd-y-ethernet-shield/)- (http://zygzax.com/2013/12/14/escribir-datos-en-una-tarjeta-sd-con-arduino-modulo-microsd-y-ethernet-shield/)modulo (http://zygzax.com/2013/12/14/escribir-datos-en-una-tarjeta-sd-con-arduino-modulo-microsd-y-ethernet-shield/)- (http://zygzax.com/2013/12/14/escribir-datos-en-una-tarjeta-sd-con-arduino-modulo-microsd-y-ethernet-shield/)microsd (http://zygzax.com/2013/12/14/escribir-datos-en-una-tarjeta-sd-con-arduino-modulo-microsd-y-ethernet-shield/)- (http://zygzax.com/2013/12/14/escribir-datos-en-una-tarjeta-sd-con-arduino-modulo-microsd-y-ethernet-shield/)y (http://zygzax.com/2013/12/14/escribir-datos-en-una-tarjeta-sd-con-arduino-modulo-microsd-y-ethernet-shield/)- (http://zygzax.com/2013/12/14/escribir-datos-en-una-tarjeta-sd-con-arduino-modulo-microsd-y-ethernet-shield/)ethernet (http://zygzax.com/2013/12/14/escribir-datos-en-una-tarjeta-sd-con-arduino-modulo-microsd-y-ethernet-shield/)- (http://zygzax.com/2013/12/14/escribir-datos-en-una-tarjeta-sd-con-arduino-modulo-microsd-y-ethernet-shield/)shield (http://zygzax.com/2013/12/14/escribir-datos-en-una-tarjeta-sd-con-arduino-modulo-microsd-y-ethernet-shield/)/ (http://zygzax.com/2013/12/14/escribir-datos-en-una-tarjeta-sd-con-arduino-modulo-microsd-y-ethernet-shield/)

Ejemplo de Software para grabar un texto en SD y Monitor serie

// Programa hecho por David Alvarez Medina (0xDA_bit) para tallerarduino.wordpress.com

// Escritura de una frase en una tarjeta SD

#include <SD.h> // Importamos libreria

// Declaracion de pins y variables de uso interno

int CS=10;

String dataString;

File dataFile;

void setup(){

Serial.begin(9600); // Establecemos comunicacion serie

Serial.println("Iniciando lectura tarjeta SD"); // Texto informativo

pinMode(CS, OUTPUT); // Declaramos el pin ChipSelect como salida

if(!SD.begin(CS)){ // Si no hay tarjeta o esta mal...

Serial.println("Tarjeta erronea o no insertada"); // Texto informativo

return;

}

Serial.println("Tarjeta OK"); // Texto informativo

}

void loop(){

dataString="tallerArduino Tutorial numero 7"; // Actualizamos la linea que guardaremos en el archivo de texto

dataFile=SD.open("log.txt", FILE_WRITE); // Creamos archivo de texto

if(dataFile){

dataFile.println(dataString); // Excribimos el contenido de "dataString" dentro del archivo de texto

dataFile.close(); // Cerramos la escritura dentro del archivo

Serial.println(dataString); // Texto informativo

}

else{

Serial.println("Escritura erronea... "); // Texto informativo

}

delay(2000); // Delay

}

Materiales

Arduino

Arduclema (http://tienda.ray-ie.com/basados-en-arduino/10-arduclema-atmega328.html)

Arduino (http://www.bricogeek.com/shop/287-arduino-screwshield.html) (http://www.bricogeek.com/shop/287-arduino-screwshield.html)Screwshield (http://www.bricogeek.com/shop/287-arduino-screwshield.html)

Interruptor Reed blindado

Caja (http://www.bricogeek.com/shop/arduino/289-caja-para-arduino.html) (http://www.bricogeek.com/shop/arduino/289-caja-para-arduino.html)para (http://www.bricogeek.com/shop/arduino/289-caja-para-arduino.html) (http://www.bricogeek.com/shop/arduino/289-caja-para-arduino.html)Arduino (http://www.bricogeek.com/shop/arduino/289-caja-para-arduino.html)

LCD (librerías Arduino):

LCDS

enlace (http://www.bricogeek.com/shop/pantallas-lcd-oled/27-pantalla-lcd-16x2-caracteres-fstn-blanco-sobre-negro.html) 1 (http://www.bricogeek.com/shop/pantallas-lcd-oled/27-pantalla-lcd-16x2-caracteres-fstn-blanco-sobre-negro.html),

Librerías:

LiquidCrystal (http://arduino.cc/es/Tutorial/LiquidCrystal)

New LiquidCrystal https (https://bitbucket.org/fmalpartida/new-liquidcrystal/wiki/Home):// (https://bitbucket.org/fmalpartida/new-liquidcrystal/wiki/Home)bitbucket (https://bitbucket.org/fmalpartida/new-liquidcrystal/wiki/Home). (https://bitbucket.org/fmalpartida/new-liquidcrystal/wiki/Home)org (https://bitbucket.org/fmalpartida/new-liquidcrystal/wiki/Home)/ (https://bitbucket.org/fmalpartida/new-liquidcrystal/wiki/Home)fmalpartida (https://bitbucket.org/fmalpartida/new-liquidcrystal/wiki/Home)/ (https://bitbucket.org/fmalpartida/new-liquidcrystal/wiki/Home)new (https://bitbucket.org/fmalpartida/new-liquidcrystal/wiki/Home)- (https://bitbucket.org/fmalpartida/new-liquidcrystal/wiki/Home)liquidcrystal (https://bitbucket.org/fmalpartida/new-liquidcrystal/wiki/Home)/ (https://bitbucket.org/fmalpartida/new-liquidcrystal/wiki/Home)wiki (https://bitbucket.org/fmalpartida/new-liquidcrystal/wiki/Home)/ (https://bitbucket.org/fmalpartida/new-liquidcrystal/wiki/Home)Home (https://bitbucket.org/fmalpartida/new-liquidcrystal/wiki/Home)

para controlar este display http (http://es.aliexpress.com/item/New-2004-204-20X4-Character-LCD-Module-Display-For-Arduino-Serial-IIC-I2C-TWI-DROP-SHIPPING/1019278159.html):// (http://es.aliexpress.com/item/New-2004-204-20X4-Character-LCD-Module-Display-For-Arduino-Serial-IIC-I2C-TWI-DROP-SHIPPING/1019278159.html)es (http://es.aliexpress.com/item/New-2004-204-20X4-Character-LCD-Module-Display-For-Arduino-Serial-IIC-I2C-TWI-DROP-SHIPPING/1019278159.html). (http://es.aliexpress.com/item/New-2004-204-20X4-Character-LCD-Module-Display-For-Arduino-Serial-IIC-I2C-TWI-DROP-SHIPPING/1019278159.html)aliexpress (http://es.aliexpress.com/item/New-2004-204-20X4-Character-LCD-Module-Display-For-Arduino-Serial-IIC-I2C-TWI-DROP-SHIPPING/1019278159.html). (http://es.aliexpress.com/item/New-2004-204-20X4-Character-LCD-Module-Display-For-Arduino-Serial-IIC-I2C-TWI-DROP-SHIPPING/1019278159.html)com (http://es.aliexpress.com/item/New-2004-204-20X4-Character-LCD-Module-Display-For-Arduino-Serial-IIC-I2C-TWI-DROP-SHIPPING/1019278159.html)/ (http://es.aliexpress.com/item/New-2004-204-20X4-Character-LCD-Module-Display-For-Arduino-Serial-IIC-I2C-TWI-DROP-SHIPPING/1019278159.html)item (http://es.aliexpress.com/item/New-2004-204-20X4-Character-LCD-Module-Display-For-Arduino-Serial-IIC-I2C-TWI-DROP-SHIPPING/1019278159.html)/ (http://es.aliexpress.com/item/New-2004-204-20X4-Character-LCD-Module-Display-For-Arduino-Serial-IIC-I2C-TWI-DROP-SHIPPING/1019278159.html)New (http://es.aliexpress.com/item/New-2004-204-20X4-Character-LCD-Module-Display-For-Arduino-Serial-IIC-I2C-TWI-DROP-SHIPPING/1019278159.html)-2004-204-20 (http://es.aliexpress.com/item/New-2004-204-20X4-Character-LCD-Module-Display-For-Arduino-Serial-IIC-I2C-TWI-DROP-SHIPPING/1019278159.html)X (http://es.aliexpress.com/item/New-2004-204-20X4-Character-LCD-Module-Display-For-Arduino-Serial-IIC-I2C-TWI-DROP-SHIPPING/1019278159.html)4- (http://es.aliexpress.com/item/New-2004-204-20X4-Character-LCD-Module-Display-For-Arduino-Serial-IIC-I2C-TWI-DROP-SHIPPING/1019278159.html)Character (http://es.aliexpress.com/item/New-2004-204-20X4-Character-LCD-Module-Display-For-Arduino-Serial-IIC-I2C-TWI-DROP-SHIPPING/1019278159.html)- (http://es.aliexpress.com/item/New-2004-204-20X4-Character-LCD-Module-Display-For-Arduino-Serial-IIC-I2C-TWI-DROP-SHIPPING/1019278159.html)LCD (http://es.aliexpress.com/item/New-2004-204-20X4-Character-LCD-Module-Display-For-Arduino-Serial-IIC-I2C-TWI-DROP-SHIPPING/1019278159.html)- (http://es.aliexpress.com/item/New-2004-204-20X4-Character-LCD-Module-Display-For-Arduino-Serial-IIC-I2C-TWI-DROP-SHIPPING/1019278159.html)Module (http://es.aliexpress.com/item/New-2004-204-20X4-Character-LCD-Module-Display-For-Arduino-Serial-IIC-I2C-TWI-DROP-SHIPPING/1019278159.html)- (http://es.aliexpress.com/item/New-2004-204-20X4-Character-LCD-Module-Display-For-Arduino-Serial-IIC-I2C-TWI-DROP-SHIPPING/1019278159.html)Display (http://es.aliexpress.com/item/New-2004-204-20X4-Character-LCD-Module-Display-For-Arduino-Serial-IIC-I2C-TWI-DROP-SHIPPING/1019278159.html)- (http://es.aliexpress.com/item/New-2004-204-20X4-Character-LCD-Module-Display-For-Arduino-Serial-IIC-I2C-TWI-DROP-SHIPPING/1019278159.html)For (http://es.aliexpress.com/item/New-2004-204-20X4-Character-LCD-Module-Display-For-Arduino-Serial-IIC-I2C-TWI-DROP-SHIPPING/1019278159.html)- (http://es.aliexpress.com/item/New-2004-204-20X4-Character-LCD-Module-Display-For-Arduino-Serial-IIC-I2C-TWI-DROP-SHIPPING/1019278159.html)Arduino (http://es.aliexpress.com/item/New-2004-204-20X4-Character-LCD-Module-Display-For-Arduino-Serial-IIC-I2C-TWI-DROP-SHIPPING/1019278159.html)- (http://es.aliexpress.com/item/New-2004-204-20X4-Character-LCD-Module-Display-For-Arduino-Serial-IIC-I2C-TWI-DROP-SHIPPING/1019278159.html)Serial (http://es.aliexpress.com/item/New-2004-204-20X4-Character-LCD-Module-Display-For-Arduino-Serial-IIC-I2C-TWI-DROP-SHIPPING/1019278159.html)- (http://es.aliexpress.com/item/New-2004-204-20X4-Character-LCD-Module-Display-For-Arduino-Serial-IIC-I2C-TWI-DROP-SHIPPING/1019278159.html)IIC (http://es.aliexpress.com/item/New-2004-204-20X4-Character-LCD-Module-Display-For-Arduino-Serial-IIC-I2C-TWI-DROP-SHIPPING/1019278159.html)- (http://es.aliexpress.com/item/New-2004-204-20X4-Character-LCD-Module-Display-For-Arduino-Serial-IIC-I2C-TWI-DROP-SHIPPING/1019278159.html)I (http://es.aliexpress.com/item/New-2004-204-20X4-Character-LCD-Module-Display-For-Arduino-Serial-IIC-I2C-TWI-DROP-SHIPPING/1019278159.html)2 (http://es.aliexpress.com/item/New-2004-204-20X4-Character-LCD-Module-Display-For-Arduino-Serial-IIC-I2C-TWI-DROP-SHIPPING/1019278159.html)C (http://es.aliexpress.com/item/New-2004-204-20X4-Character-LCD-Module-Display-For-Arduino-Serial-IIC-I2C-TWI-DROP-SHIPPING/1019278159.html)- (http://es.aliexpress.com/item/New-2004-204-20X4-Character-LCD-Module-Display-For-Arduino-Serial-IIC-I2C-TWI-DROP-SHIPPING/1019278159.html)TWI (http://es.aliexpress.com/item/New-2004-204-20X4-Character-LCD-Module-Display-For-Arduino-Serial-IIC-I2C-TWI-DROP-SHIPPING/1019278159.html)- (http://es.aliexpress.com/item/New-2004-204-20X4-Character-LCD-Module-Display-For-Arduino-Serial-IIC-I2C-TWI-DROP-SHIPPING/1019278159.html)DROP (http://es.aliexpress.com/item/New-2004-204-20X4-Character-LCD-Module-Display-For-Arduino-Serial-IIC-I2C-TWI-DROP-SHIPPING/1019278159.html)- (http://es.aliexpress.com/item/New-2004-204-20X4-Character-LCD-Module-Display-For-Arduino-Serial-IIC-I2C-TWI-DROP-SHIPPING/1019278159.html)SHIPPING (http://es.aliexpress.com/item/New-2004-204-20X4-Character-LCD-Module-Display-For-Arduino-Serial-IIC-I2C-TWI-DROP-SHIPPING/1019278159.html)/1019278159. (http://es.aliexpress.com/item/New-2004-204-20X4-Character-LCD-Module-Display-For-Arduino-Serial-IIC-I2C-TWI-DROP-SHIPPING/1019278159.html)html (http://es.aliexpress.com/item/New-2004-204-20X4-Character-LCD-Module-Display-For-Arduino-Serial-IIC-I2C-TWI-DROP-SHIPPING/1019278159.html)

Módulos conectar y listo

Electan:

http (http://www.electan.com/mobile_product_info.php?cPath=345&products_id=3043):// (http://www.electan.com/mobile_product_info.php?cPath=345&products_id=3043)www (http://www.electan.com/mobile_product_info.php?cPath=345&products_id=3043). (http://www.electan.com/mobile_product_info.php?cPath=345&products_id=3043)electan (http://www.electan.com/mobile_product_info.php?cPath=345&products_id=3043). (http://www.electan.com/mobile_product_info.php?cPath=345&products_id=3043)com (http://www.electan.com/mobile_product_info.php?cPath=345&products_id=3043)/ (http://www.electan.com/mobile_product_info.php?cPath=345&products_id=3043)mobile (http://www.electan.com/mobile_product_info.php?cPath=345&products_id=3043)_ (http://www.electan.com/mobile_product_info.php?cPath=345&products_id=3043)product (http://www.electan.com/mobile_product_info.php?cPath=345&products_id=3043)_ (http://www.electan.com/mobile_product_info.php?cPath=345&products_id=3043)info (http://www.electan.com/mobile_product_info.php?cPath=345&products_id=3043). (http://www.electan.com/mobile_product_info.php?cPath=345&products_id=3043)php (http://www.electan.com/mobile_product_info.php?cPath=345&products_id=3043)? (http://www.electan.com/mobile_product_info.php?cPath=345&products_id=3043)cPath (http://www.electan.com/mobile_product_info.php?cPath=345&products_id=3043)=345& (http://www.electan.com/mobile_product_info.php?cPath=345&products_id=3043)products (http://www.electan.com/mobile_product_info.php?cPath=345&products_id=3043)_ (http://www.electan.com/mobile_product_info.php?cPath=345&products_id=3043)id (http://www.electan.com/mobile_product_info.php?cPath=345&products_id=3043)=3043 (http://www.electan.com/mobile_product_info.php?cPath=345&products_id=3043)

http (http://www.electan.com/mobile_product_info.php?cPath=345&products_id=2999):// (http://www.electan.com/mobile_product_info.php?cPath=345&products_id=2999)www (http://www.electan.com/mobile_product_info.php?cPath=345&products_id=2999). (http://www.electan.com/mobile_product_info.php?cPath=345&products_id=2999)electan (http://www.electan.com/mobile_product_info.php?cPath=345&products_id=2999). (http://www.electan.com/mobile_product_info.php?cPath=345&products_id=2999)com (http://www.electan.com/mobile_product_info.php?cPath=345&products_id=2999)/ (http://www.electan.com/mobile_product_info.php?cPath=345&products_id=2999)mobile (http://www.electan.com/mobile_product_info.php?cPath=345&products_id=2999)_ (http://www.electan.com/mobile_product_info.php?cPath=345&products_id=2999)product (http://www.electan.com/mobile_product_info.php?cPath=345&products_id=2999)_ (http://www.electan.com/mobile_product_info.php?cPath=345&products_id=2999)info (http://www.electan.com/mobile_product_info.php?cPath=345&products_id=2999). (http://www.electan.com/mobile_product_info.php?cPath=345&products_id=2999)php (http://www.electan.com/mobile_product_info.php?cPath=345&products_id=2999)? (http://www.electan.com/mobile_product_info.php?cPath=345&products_id=2999)cPath (http://www.electan.com/mobile_product_info.php?cPath=345&products_id=2999)=345& (http://www.electan.com/mobile_product_info.php?cPath=345&products_id=2999)products (http://www.electan.com/mobile_product_info.php?cPath=345&products_id=2999)_ (http://www.electan.com/mobile_product_info.php?cPath=345&products_id=2999)id (http://www.electan.com/mobile_product_info.php?cPath=345&products_id=2999)=2999 (http://www.electan.com/mobile_product_info.php?cPath=345&products_id=2999)

Compra Dx.com

Thursday, 12 December 2013 17:35 | Home (http://www.dx.com/) (http://www.dx.com/)| Help (http://help.dx.com/)

Dear Pedro,

Order No.: 131212001041392787 (https://my.dx.com/MyOrders/OrderDetail/131212001041392787) | Order Date: Thursday, 12 December 2013 17:35

Thank you for ordering from DX (http://www.dx.com/). (http://www.dx.com/)com (http://www.dx.com/).

Your order has been successfully created and the transaction is being processed.

If the payment for your order was processed successfully, you can check your order status by clicking My (https://my.dx.com/MyOrders/Index) (https://my.dx.com/MyOrders/Index)Orders (https://my.dx.com/MyOrders/Index) from your DX account.

You will receive a notification email from us once your transaction is confirmed.

Please confirm your order details and shipping address as below:

Item(s) | Purchase Price | Discount | Gift Qty | Qty | LineTotalPrice
LCD (http://www.dx.com/p/118059) (http://www.dx.com/p/118059)Keypad (http://www.dx.com/p/118059) (http://www.dx.com/p/118059)Shield (http://www.dx.com/p/118059) (http://www.dx.com/p/118059)for (http://www.dx.com/p/118059) (http://www.dx.com/p/118059)Arduino (http://www.dx.com/p/118059) (http://www.dx.com/p/118059)Duemilanove (http://www.dx.com/p/118059) & (http://www.dx.com/p/118059)LCD (http://www.dx.com/p/118059) 1602 ( (http://www.dx.com/p/118059)Works (http://www.dx.com/p/118059) (http://www.dx.com/p/118059)with (http://www.dx.com/p/118059) (http://www.dx.com/p/118059)Official (http://ww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 | US$ 6.40 | US$ 0.00 | 0 | 1 | US$ 6.40
1602 (http://www.dx.com/p/151978)A (http://www.dx.com/p/151978) 16 (http://www.dx.com/p/151978)x (http://www.dx.com/p/151978) 2 (http://www.dx.com/p/151978)Lines (http://www.dx.com/p/151978) (http://www.dx.com/p/151978)White (http://www.dx.com/p/151978) (http://www.dx.com/p/151978)Character (http://www.dx.com/p/151978) (http://www.dx.com/p/151978)LCD (http://www.dx.com/p/151978) (http://www.dx.com/p/151978)Module (http://www.dx.com/p/151978) (http://www.dx.com/p/151978)w (http://www.dx.com/p/151978)/ (http://www.dx.com/p/151978)Blue (http://www.dx.com/p/151978) (http://www.dx.com/p/151978)Ba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 | US$ 3.50 | US$ 0.00 | 0 | 1 | US$ 3.50
Sensor (http://www.dx.com/p/66849) (http://www.dx.com/p/66849)Shield (http://www.dx.com/p/66849) (http://www.dx.com/p/66849)V (http://www.dx.com/p/66849)4.0 (http://www.dx.com/p/66849)for (http://www.dx.com/p/66849) (http://www.dx.com/p/66849)Arduino (http://www.dx.com/p/66849) ( (http://www.dx.com/p/66849)Works (http://www.dx.com/p/66849) (http://www.dx.com/p/66849)with (http://www.dx.com/p/66849) (http://www.dx.com/p/66849)Official (http://www.dx.com/p/66849) (http://www.dx.com/p/66849)Arduino (http://www.dx.com/p/66849) (http://www.dx.com/p/66849)Boards (http://www.dx.com/p/66849))-66849 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 | US$ 4.70 | US$ 0.00 | 0 | 1 | US$ 4.70
Hall (http://www.dx.com/p/141363) (http://www.dx.com/p/141363)Magnetic (http://www.dx.com/p/141363) (http://www.dx.com/p/141363)Sensor (http://www.dx.com/p/141363) / (http://www.dx.com/p/141363)Switch (http://www.dx.com/p/141363) (http://www.dx.com/p/141363)Module (http://www.dx.com/p/141363) (http://www.dx.com/p/141363)for (http://www.dx.com/p/141363) (http://www.dx.com/p/141363)Smart (http://www.dx.com/p/141363) (http://www.dx.com/p/141363)Car (http://www.dx.com/p/141363)-141363 (http://www.dx.com/p/141363) | US$ 6.10 | US$ 0.00 | 0 | 1 | US$ 6.10
Breadboard (http://www.dx.com/p/80208) (http://www.dx.com/p/80208)Jumper (http://www.dx.com/p/80208) (http://www.dx.com/p/80208)Wires (http://www.dx.com/p/80208) (http://www.dx.com/p/80208)for (http://www.dx.com/p/80208) (http://www.dx.com/p/80208)Electronic (http://www.dx.com/p/80208) (http://www.dx.com/p/80208)DIY (http://www.dx.com/p/80208) (70- (http://www.dx.com/p/80208)Cable (http://www.dx.com/p/80208) (http://www.dx.com/p/80208)Pack (http://www.dx.com/p/80208))-80208 (http://www.dx.com/p/80208) | US$ 3.17 | US$ 0.00 | 0 | 1 | US$ 3.17

| | GoodsTotal: | US$23.87
ShippingFee Discount: | US$1.70 | ShippingFee: | US$0.00
| | TotalAmount: | US$25.57
Grand Total: US$23.87

Otras webs

http (http://tallerarduino.com):// (http://tallerarduino.com)tallerarduino (http://tallerarduino.com). (http://tallerarduino.com)com (http://tallerarduino.com)

http (http://arduinolab.wordpress.com/):// (http://arduinolab.wordpress.com/)arduinolab (http://arduinolab.wordpress.com/). (http://arduinolab.wordpress.com/)wordpress (http://arduinolab.wordpress.com/). (http://arduinolab.wordpress.com/)com (http://arduinolab.wordpress.com/)/ (http://arduinolab.wordpress.com/)

http (http://forum.arduino.cc/index.php?topic=68353.5;wap2):// (http://forum.arduino.cc/index.php?topic=68353.5;wap2)forum (http://forum.arduino.cc/index.php?topic=68353.5;wap2). (http://forum.arduino.cc/index.php?topic=68353.5;wap2)arduino (http://forum.arduino.cc/index.php?topic=68353.5;wap2). (http://forum.arduino.cc/index.php?topic=68353.5;wap2)cc (http://forum.arduino.cc/index.php?topic=68353.5;wap2)/ (http://forum.arduino.cc/index.php?topic=68353.5;wap2)index (http://forum.arduino.cc/index.php?topic=68353.5;wap2). (http://forum.arduino.cc/index.php?topic=68353.5;wap2)php (http://forum.arduino.cc/index.php?topic=68353.5;wap2)? (http://forum.arduino.cc/index.php?topic=68353.5;wap2)topic (http://forum.arduino.cc/index.php?topic=68353.5;wap2)=68353.5; (http://forum.arduino.cc/index.php?topic=68353.5;wap2)wap (http://forum.arduino.cc/index.php?topic=68353.5;wap2)2 (http://forum.arduino.cc/index.php?topic=68353.5;wap2) Problema con velocímetro

Quizá esto sirva de ayuda para el truncamiento: http://forum.arduino.cc/index.php?topic=208565.0

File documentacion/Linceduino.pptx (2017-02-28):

## Linceduino

Ayuda electrónica para el LINCE

## Contexto

- Curso: 2º de Bachillerato.
- Materia: Proyecto Integrado (Robótica)
- IES Pedro Soto de Rojas (Granada)

## ¿Lince?

Ayudamos a el LINCE: Proyecto increíble de vehículo ecológico que participa en ECO-Shell Marathon. Único equipo de Bachillerato de Europa. Son Andaluces (Andújar).
http://lince-jandula.blogspot.com.es/


## Problema

- El equipo del Lince tiene problemas serios de retardo de muestra de datos con velocímetros de bicicleta.
- Nos propone que lo solucionemos.

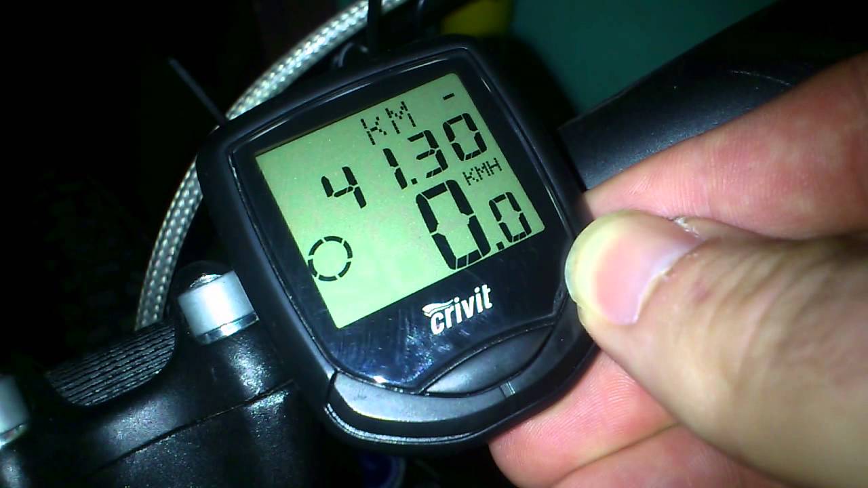
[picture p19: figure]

## Solución. Linceduino

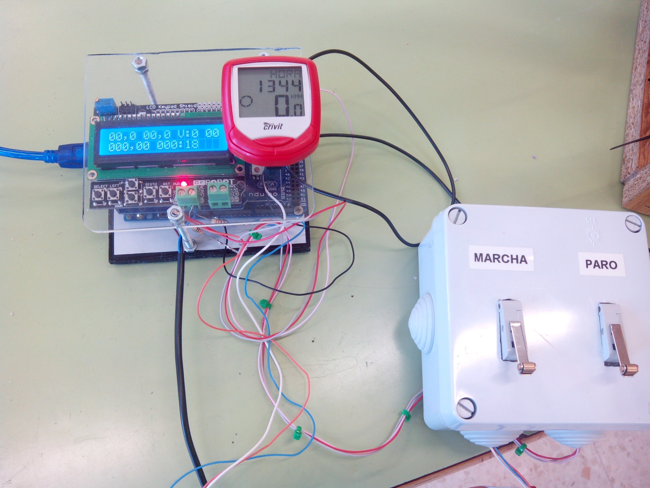
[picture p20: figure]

## ¿Qué realiza?

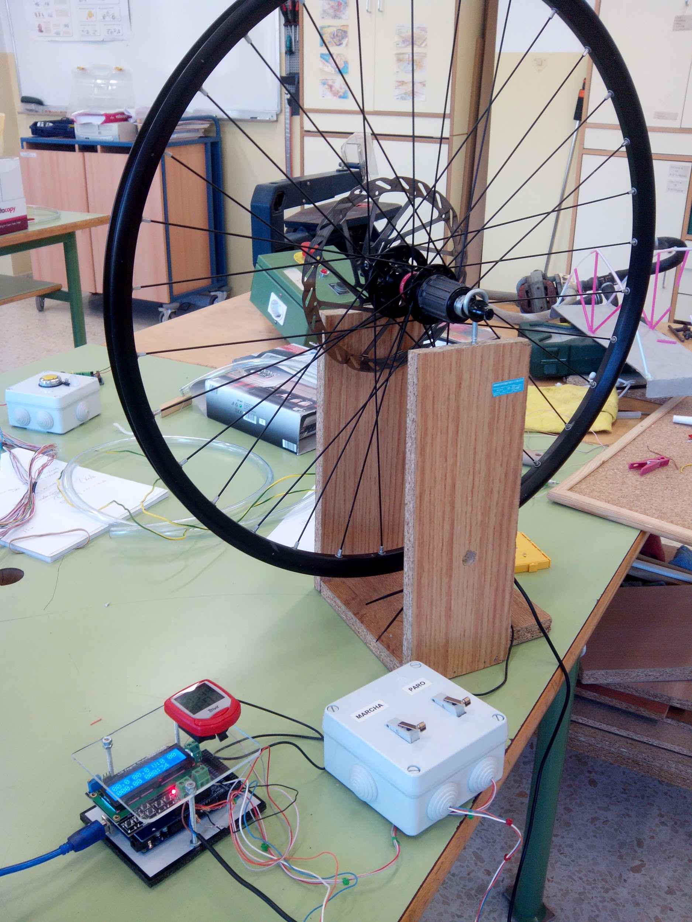
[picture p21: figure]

Muestra en pantalla y graba en tarjeta SD:
- Velocidad instantánea.
- Velocidad media.
- Nº de vueltas a circuito.
- Distancia recorrida.
- Tiempo transcurrido.
- Pulsaciones de marcha y paro de motor.

## Vídeo

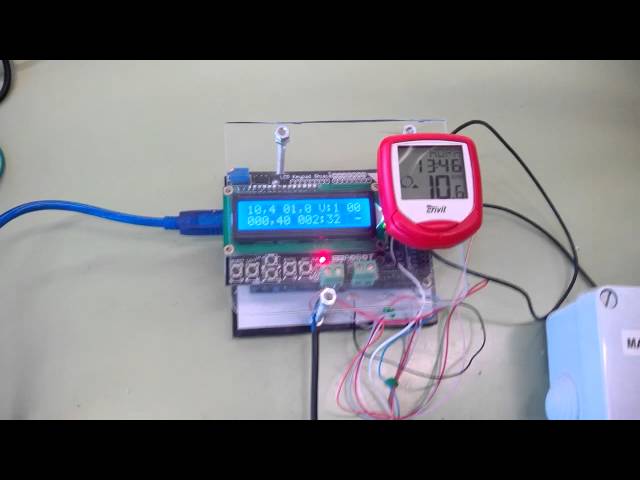
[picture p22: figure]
Proyecto de medidor y grabador electrónico para el Lince programado con Arduino Mega. Realizado por Pablo Baeyens y Santiago Vidal com colaboración del grupo de proyecto integrado de robótica de 2º de Bachillerato.

## Telemetría

Los datos de telemetría son fundamentales para las estrategias de bajo consumo.
Linceduino exporta los datos de SD a hoja de cálculo para que sean interpretados.

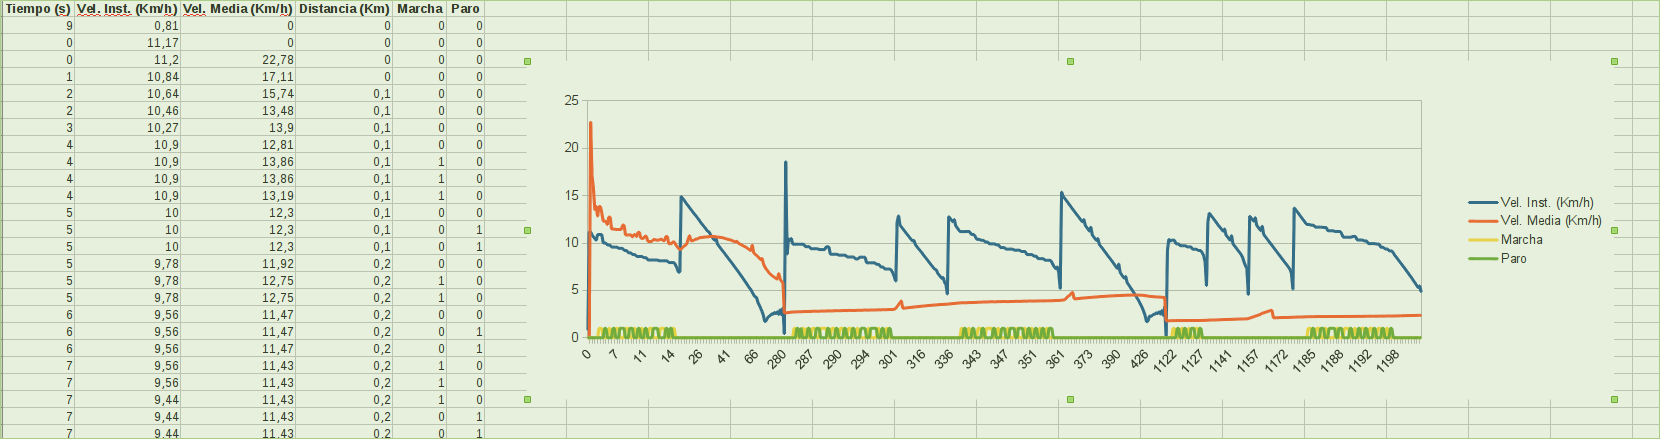
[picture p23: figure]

## Hardware

El hardware está compuesto por:
Arduino Mega + SD Shield + LCD Keypad Shield

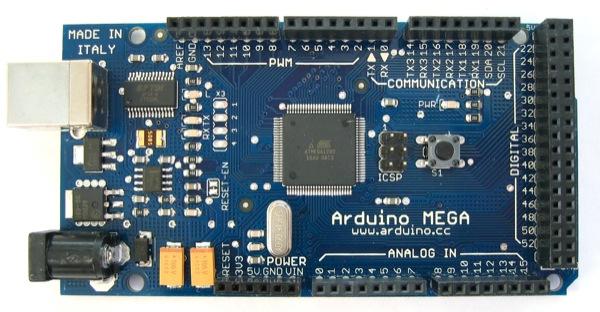
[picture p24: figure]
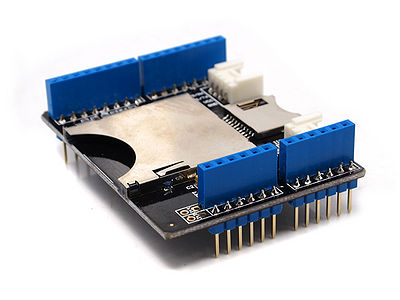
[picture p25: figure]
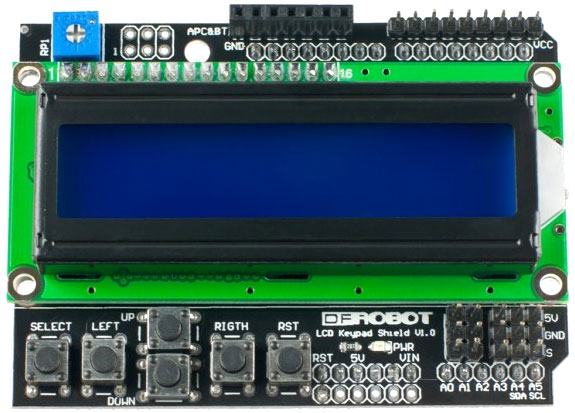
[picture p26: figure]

## Software

Está programado con el software de Arduino, y está gobernado por interrupciones, de tal modo que muestra en pantalla información y graba en la SD cada vez que el imán de la rueda excita a el sensor hall (magnético) o cada vez que el piloto pulsa los interruptores de marcha o paro del motor.
Graba en la SD 10000 registros en el transcurso de la prueba del lince.

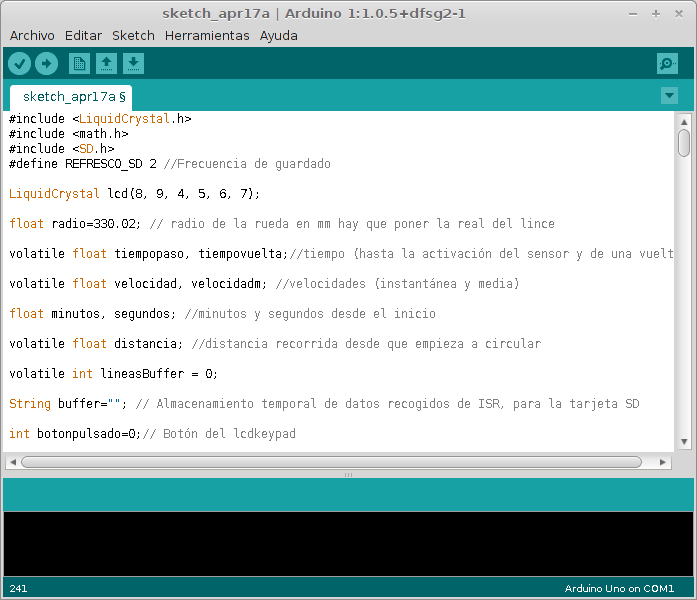
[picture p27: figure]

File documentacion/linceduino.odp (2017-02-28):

## Linceduino

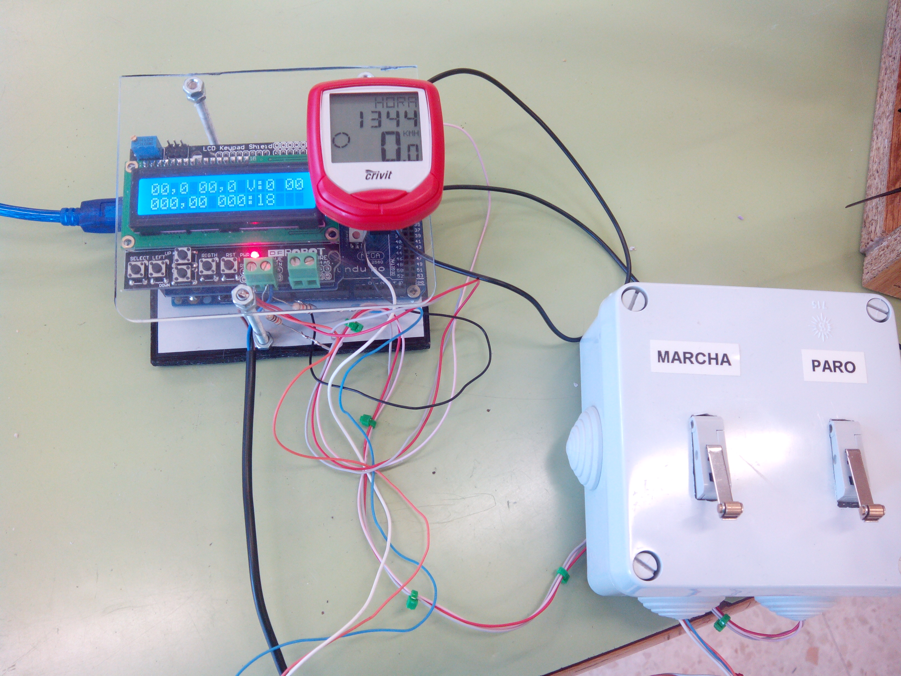
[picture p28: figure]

Ayuda electrónica para el LINCE

## Contexto

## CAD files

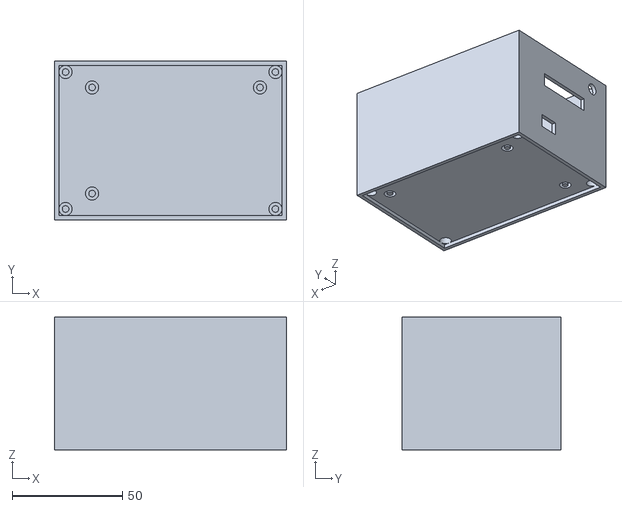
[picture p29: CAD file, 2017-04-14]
linceduino_caja/linceduino_bottom.stl
105.0 x 72.0 x 60.0

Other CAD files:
linceduino_caja/linceduino_bottom.skp

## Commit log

2015-04-30 Create lunceduino2 con solo pulsador de marcha
2015-04-30 Update lunceduino2 con solo pulsador de marcha
2017-02-28 añadimos carpeta de imágenes
2017-02-28 añadidos diseños de prueba
2017-02-28 añadidas imágenes y archivos sobre organización de alumnado
2017-02-28 empieza el desarrollo de la documentación
2017-02-28 añadidos archivos de documentación e imágenes de linceduino 1
2017-03-31 cambios en el README
2017-04-08 pequeños cambios en manual de uso
2017-04-08 añadidos contenidos sobre la visualización de datos con kst
2017-04-08 añadida carpeta con los archivos fundamentales para kst
2017-04-14 añadido diseño de caja
    [linceduino_bottom.skp, linceduino_bottom.stl]
2017-05-04 añadido nueva versión 2.2 de Linceduino
2017-05-21 añadidos los programas de las versiones 2.1.1 y 2.2.1 mejoras en sangrado y control de velocidad instantánea por encima de 100 km/h
